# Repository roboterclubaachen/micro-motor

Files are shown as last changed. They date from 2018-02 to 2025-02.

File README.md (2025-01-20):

# µMotor: a motor controller for BLDC and DC motors up to 250W

µMotor (or micro-motor) is a motor controller PCB and software made to control any BLDC and DC motor up to 250W.

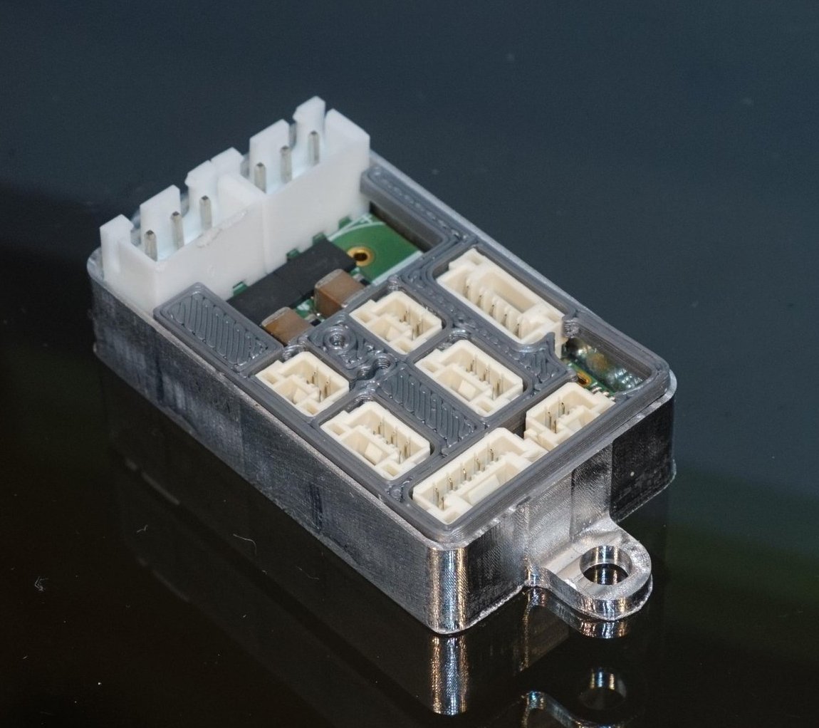
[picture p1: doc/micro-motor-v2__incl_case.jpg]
Image of micro-motor-v2 PCB in a milled aluminium case


The micro-motor is supplied with power and CAN bus via a single connector and can control the motor independently.
In addition, a limit switch can be read out and the temperature of the motor can be monitored.

Communication is done via Can-Bus using CANopen protocol.

The software is written using the [modm.io](https://modm.io/) framework and [librobots2](https://github.com/roboterclubaachen/librobots2).

For more information read the following blog posts about the project (in German):
* [µMotor: Idee](http://www.roboterclub.rwth-aachen.de/blog/2018/micro-motor-motorcontroller.html)
* [µMotor: Inbetriebnahme und Debugging](http://www.roboterclub.rwth-aachen.de/blog/2018/micro-motor-debugging-inbetriebnahme.html)
* [µMotor 2 - Teil 1: Konzept](http://www.roboterclub.rwth-aachen.de/blog/2019/micro-motor-2-teil-1.html)
* [µMotor 2 - Teil 2: Strommessung](http://www.roboterclub.rwth-aachen.de/blog/2019/micro-motor-2-teil-2.html)
* [µMotor 2 - Teil 3: Microcontroller & Stromversorgung](http://www.roboterclub.rwth-aachen.de/blog/2019/micro-motor-2-teil-3.html)
* [µMotor 2 - Teil 4: Strom- und Spannungsmessung mit ADC](https://www.roboterclub.rwth-aachen.de/blog/2020/micro-motor-2-teil-4.html)

## Technical data
* 3 phases (BLDC and DC motors)
* Approx. 10A per phase (with precise current measurement)
* 24V nominal operating voltage
* Adjustable cycle-by-cycle current limiting (short circuit protection)
* CAN bus
    * CAN-FD supported
    * CANopen protocoll (partial implemented)
* AB(I) incremental encoder connector
* Hall sensor connector
* Temperature sensor (NTC) connector
* Limit switch (GPIO) connector
* LEDs for status and diagnosis
* Configurable ID (from STM32 hardware ID)
* Easy to solder and assemble

## Status

PCBs *micro-motor-v1 (rev1)* and *macro-motor* are not supported anymore.

The second version *micro-motor-v2* is basically functional, software improvements are in progress.

PCB _micro-motor-v2.1_ is similar to _v2_, but with added RC filters at encoder connector,
added 1 µF capacitor to the STM32 _VREFBUF_ output and changed DC/DC converter modules (caused by component shortage).

Software at HEAD is compatible with micro-motor-v2.\[0,1,2\], however the correct version needs to be selected in the project.xml to account for hardware differences with "Board.v2_1" being compatible with v2.0, and v2.1 and "Board.v2_2" being compatible with v2.2.

## Folder structure

#### `kicad/pcb_name/`
* KiCad files of the PCBs

#### `STM32CubeMX/`
* Pinout configuration of the STM32 microcontrollers done with [STs CubeMX software](https://www.st.com/en/development-tools/stm32cubemx.html)

#### `tests/`
* Test software. Useful during PCB assembly

#### `app/`
* Main Software

#### `src/`
* Common files used between main software and tests.

## Notes

### On first boot
When first assembled the boards will be stuck inside the STM32 bootloader because BOOT0 is used as a GPIO pin.
This behaviour can be overwritten by setting an option byte: \
First read flash option byte:

    openocd -f interface/stlink.cfg -c "transport select hla_swd" -f target/stm32g4x.cfg -c "reset_config none" -c "init" -c "stm32g4x option_read 0 0x20" -c "shutdown"

Should respond 'Option Register: <0x40022020> = 0xffeff8aa' on a new PCB
or 'Option Register: <0x40022020> = 0xfbeff8aa' once the nSWBOOT0 bit is cleared. \
Clear the bit:

    openocd -f interface/stlink.cfg -c "transport select hla_swd" -f target/stm32g4x.cfg -c "reset_config none" -c "init" -c "stm32g4x option_write 0 0x20 0x00000000 0x04000000" -c "shutdown"

## License

Software is licensed under [GPLv3](LICENSE).
Hardware (PCB files, ...) is licensed under [CERN OHL v.1.2](LICENSE.hardware).

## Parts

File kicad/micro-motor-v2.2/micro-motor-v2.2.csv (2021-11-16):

Id | Designator | Package | Quantity | Designation | Supplier and ref
1 | U502 | Texas_SIL0010A_MicroSiP-10-1EP_3.8x3mm_P0.6mm_EP0.7x2.9mm | 1 | LMZM23601V5
2 | U501 | Texas_SIL0010A_MicroSiP-10-1EP_3.8x3mm_P0.6mm_EP0.7x2.9mm | 1 | LMZM23601V3
3 | R117,R116,R115 | R_0402_1005Metric | 3 | 10R
4 | C307 | C_0402_1005Metric | 1 | 1u
5 | C103,C102,C101 | C_0402_1005Metric | 3 | 10n
6 | U401 | QFN-32-1EP_5x5mm_P0.5mm_EP3.45x3.45mm | 1 | DRV8320S
7 | R114 | R_0402_1005Metric | 1 | 0
8 | C401 | CP_Radial_D10.0mm_P5.00mm | 1 | >10µ 35V
9 | C409,C408,C407 | C_1210_3225Metric | 3 | 22µ 35V 1210
10 | C412,C411,C410,C201,C403,C402,C306,C305,C304,C303,C302,C301 | C_0402_1005Metric | 12 | 100n
11 | R113,R112,R111,R401,R108,R101 | R_0402_1005Metric | 6 | 10k
12 | C502,C501,C504,C503 | C_0805_2012Metric | 4 | 22µ 10V 0805
13 | U404,U403,U402 | TSSOP-8_4.4x3mm_P0.65mm | 3 | INA240A2PW
14 | U301 | LQFP-48_7x7mm_P0.5mm | 1 | STM32G474CET6
15 | U201 | SOT-23-8 | 1 | TCAN332
16 | TP303 | TestPoint_Pad_D1.0mm | 1 | BK
17 | TP302 | TestPoint_Pad_D1.0mm | 1 | DAC1
18 | TP301 | TestPoint_Pad_D1.0mm | 1 | DAC2
19 | TP103 | TestPoint_Pad_D1.0mm | 1 | W
20 | TP102 | TestPoint_Pad_D1.0mm | 1 | V
21 | TP101 | TestPoint_Pad_D1.0mm | 1 | U
22 | R404,R403,R402 | R_0805_2012Metric | 3 | 5m
23 | R306,R305,R304,R110,R107,R105,R103 | R_0402_1005Metric | 7 | 1k
24 | R109,R106,R104,R102 | R_0402_1005Metric | 4 | 20k
25 | Q403,Q402,Q401 | DFN-12-2EP_3.3x5mm_Pitch0.65mm | 3 | FDMD82xx
26 | J303 | JST_GH_BM03B-GHS-TBT_1x03-1MP_P1.25mm_Vertical | 1 | SWD
27 | J302 | JST_GH_BM03B-GHS-TBT_1x03-1MP_P1.25mm_Vertical | 1 | UART
28 | J301 | USB_Micro-B_Molex-105133-0001 | 1 | USB
29 | J201 | JST_GH_BM02B-GHS-TBT_1x02-1MP_P1.25mm_Vertical | 1 | CAN
30 | J106 | JST_XH_B3B-XH-A_1x03_P2.50mm_Vertical | 1 | Motor
31 | J105 | JST_GH_BM02B-GHS-TBT_1x02-1MP_P1.25mm_Vertical | 1 | NTC
32 | J104 | JST_GH_BM05B-GHS-TBT_1x05-1MP_P1.25mm_Vertical | 1 | Encoder
33 | J103 | JST_GH_BM05B-GHS-TBT_1x05-1MP_P1.25mm_Vertical | 1 | Hall
34 | J102 | JST_GH_BM02B-GHS-TBT_1x02-1MP_P1.25mm_Vertical | 1 | SW
35 | J101 | JST_XH_B3B-XH-A_1x03_P2.50mm_Vertical | 1 | SUPPLY
36 | D303 | LED_0402_1005Metric | 1 | DAC2/green
37 | D302 | LED_0402_1005Metric | 1 | DAC1/red
38 | D301 | LED_0402_1005Metric | 1 | POWER/blue
39 | C406 | C_0402_1005Metric | 1 | 47n 50V X7R
40 | C405 | C_0603_1608Metric | 1 | 1µ 16V X7R
41 | C404 | C_0603_1608Metric | 1 | 1µ 6V3 X7R

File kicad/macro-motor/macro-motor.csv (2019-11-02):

Id | Designator | Package | Quantity | Designation | Supplier and ref
1 | REF**,REF**,REF**,REF** | MountingHole_3.2mm_M3_DIN965_Pad | 4 | MountingHole_3.2mm_M3_DIN965_Pad
2 | C201,C401,C601,C602,C603,C501,C206 | C_0402_1005Metric | 7 | 100n
3 | J604 | PinHeader_1x03_P2.54mm_Vertical | 1 | UART
4 | C101 | C_0603_1608Metric | 1 | 4µ7 16V
5 | C102,C103 | C_0402_1005Metric | 2 | 2µ2 6V3
6 | C301 | CP_Radial_D8.0mm_P3.50mm | 1 | >10µ 35V
7 | C302 | C_0603_1608Metric | 1 | 100n 50V
8 | C303 | C_0402_1005Metric | 1 | 100n 50V
9 | C304 | C_0402_1005Metric | 1 | 1µ 6V3 X7R
10 | C305 | C_0402_1005Metric | 1 | 1µ 16V X7R
11 | C306 | C_0402_1005Metric | 1 | 47n 50V X7R
12 | D601 | LED_0402_1005Metric | 1 | Blue
13 | D602 | LED_0402_1005Metric | 1 | Red
14 | J101 | PinHeader_1x05_P2.54mm_Vertical | 1 | CAN+PWR
15 | J102,J503 | Pin_D1.0mm_L10.0mm | 2 | 3V3
16 | J103 | Pin_D1.0mm_L10.0mm | 1 | 5V
17 | J104,J504,TP302 | Pin_D1.0mm_L10.0mm | 3 | GND
18 | J105 | Pin_D1.0mm_L10.0mm | 1 | Gpio
19 | J106,TP315,TP324 | Pin_D1.0mm_L10.0mm | 3 | U
20 | J107,TP314,TP323 | Pin_D1.0mm_L10.0mm | 3 | V
21 | J108,TP313,TP322 | Pin_D1.0mm_L10.0mm | 3 | W
22 | J109 | TerminalBlock_Phoenix_PT-1,5-3-3.5-H_1x03_P3.50mm_Horizontal | 1 | Conn_01x03_Female
23 | J202 | Pin_D1.0mm_L10.0mm | 1 | B
24 | J203 | Pin_D1.0mm_L10.0mm | 1 | A
25 | J301 | PinHeader_1x02_P2.54mm_Vertical | 1 | A
26 | J302 | PinHeader_1x02_P2.54mm_Vertical | 1 | B
27 | J303 | PinHeader_1x02_P2.54mm_Vertical | 1 | C
28 | J501 | Pin_D1.0mm_L10.0mm | 1 | SCL
29 | J502 | Pin_D1.0mm_L10.0mm | 1 | SDA
30 | J601 | PinHeader_1x03_P2.54mm_Vertical | 1 | SWD
31 | J605 | Pin_D1.0mm_L10.0mm | 1 | OP_INM
32 | J606 | Pin_D1.0mm_L10.0mm | 1 | OP_OUT
33 | J607 | Pin_D1.0mm_L10.0mm | 1 | PA0
34 | J608 | Pin_D1.0mm_L10.0mm | 1 | PH1
35 | J609 | Pin_D1.0mm_L10.0mm | 1 | PH0
36 | JP301 | SolderJumper-2_P1.3mm_Open_RoundedPad1.0x1.5mm | 1 | SPC
37 | JP302 | SolderJumper-2_P1.3mm_Open_RoundedPad1.0x1.5mm | 1 | SPB
38 | JP303 | SolderJumper-2_P1.3mm_Open_RoundedPad1.0x1.5mm | 1 | SPA
39 | Q301,Q302,Q303 | DFN-12-2EP_3.3x5mm_Pitch0.65mm | 3 | FDMD82xx
40 | R101,R301,R603,R605,R606,R607,R608 | R_0402_1005Metric | 7 | 10k
41 | R102,R103,R104,R601,R602,R604 | R_0402_1005Metric | 6 | 1k
42 | R105,R106,R107 | R_0402_1005Metric | 3 | 20k
43 | R302,R303,R304 | R_0805_2012Metric | 3 | 5m
44 | R501,R502 | R_0402_1005Metric | 2 | 4k7
45 | TP303,TP304 | Pin_D1.0mm_L10.0mm | 2 | UP
46 | TP305 | Pin_D1.0mm_L10.0mm | 1 | VP
47 | TP306 | Pin_D1.0mm_L10.0mm | 1 | VN
48 | TP307 | Pin_D1.0mm_L10.0mm | 1 | WP
49 | TP308 | Pin_D1.0mm_L10.0mm | 1 | WN
50 | TP309 | Pin_D1.0mm_L10.0mm | 1 | MOSI
51 | TP310 | Pin_D1.0mm_L10.0mm | 1 | MISO
52 | TP311 | Pin_D1.0mm_L10.0mm | 1 | SCK
53 | TP312 | Pin_D1.0mm_L10.0mm | 1 | ~CS
54 | TP316 | Pin_D1.0mm_L10.0mm | 1 | GH_U
55 | TP317 | Pin_D1.0mm_L10.0mm | 1 | GL_U
56 | TP318 | Pin_D1.0mm_L10.0mm | 1 | GH_W
57 | TP319 | Pin_D1.0mm_L10.0mm | 1 | GL_W
58 | TP320 | Pin_D1.0mm_L10.0mm | 1 | GH_V
59 | TP321 | Pin_D1.0mm_L10.0mm | 1 | GL_V
60 | U101 | WLCSP-6_1.4x1.0mm_P0.4mm | 1 | ADP7112ACBZ-3.3-R7
61 | U102 | WLCSP-6_1.4x1.0mm_P0.4mm | 1 | ADP7112ACBZ-5.0-R7
62 | U301 | QFN-40-1EP_6x6mm_P0.5mm_EP4.6x4.6mm | 1 | DRV8323S
63 | U401 | SOT-23-8 | 1 | TCAN330
64 | U501 | WCSP-8_1.6x1.6mm_P0.5mm | 1 | TMP006
65 | U601 | QFN-48-1EP_7x7mm_P0.5mm_EP5.6x5.6mm | 1 | STM32L433C(B-C)Ux_u
66 | J110 | PinHeader_1x05_P2.54mm_Vertical | 1 | HALL
67 | J204 | PinHeader_1x06_P2.54mm_Vertical | 1 | Encoder
68 | R203,R204,R205,R206 | R_0402_1005Metric | 4 | 47k
69 | TP301 | Pin_D1.0mm_L10.0mm | 1 | +24V
70 | J111 | Pin_D1.0mm_L10.0mm | 1 | Fault
71 | R108 | R_0402_1005Metric | 1 | (10k)
72 | C202,C203,C204,C205 | C_0402_1005Metric | 4 | (2n7)
73 | RN201 | EXB18V | 1 | (2k7)
74 | RN202 | EXB18V | 1 | (100)
75 | G*** | aisler-logo | 1 | LOGO
76 | G*** | rca-logo | 1 | LOGO
77 | U201,U202 | SOT-23-5 | 2 | ISL3280E

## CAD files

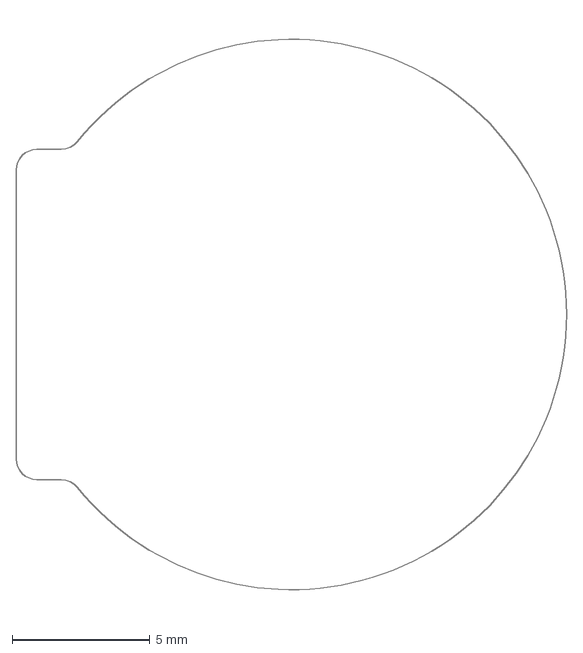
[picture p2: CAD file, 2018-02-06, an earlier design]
kicad/micro-motor-v1/PCB_Outline_rev1.dxf
20.0 x 21.7 mm

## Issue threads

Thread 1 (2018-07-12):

Bug in PCB rev1 // TODO for PCB rev2

rleh, 2018-07-12:
* [ ] SPI MISO pull-up resistor (10k)
* [ ] ~I²C pull-up resistors (4k7)~
* [ ] Analog (NTC) temperature sensor instead of I²C
* [ ] Measure (ADC) or detect (GPIO) the input voltage from STM32
* [ ] Remove integrated magnet encoder
* [ ] ~THT terminals~ Small SMD connectors (e.g. [JST GH](https://jst.de/product-family/show/89/gh))
  * [ ] Encoder (A, B, I, GND, 5V|3.3V)
  * [ ] Hall sensor (U, V, W, GND, 5V|3.3V)
  * [ ] End switch
  * [ ] CAN?
* [ ] Power connectors (e.g. [JST XH](https://jst.de/product-family/show/184/xh))
  * [ ]  Power supply: 20V, 6V, GND; >=5A
  * [ ] Combined with CAN?
* [ ] Use MOSFET R_dson (4..6mΩ) instead of 5mΩ shunt resistor?
* [ ] NCP4623 is *NRND* -> Replacement: [ADP7112](http://www.analog.com/media/en/technical-documentation/data-sheets/ADP7112.pdf) *1mm × 1.2mm, 6-ball WLCSP*
  * [ ] Discussion: [Fully integrated switching regulator TPS82150](http://www.ti.com/product/TPS82150) for 5V (and 3.3V)?
* [ ] Mechanical dimensions: ~Round~ Rectangular shape, approx. 15x25mm²

To be continued...

rleh, 2021-07-31:
Done.

Closed 2021-07-31.

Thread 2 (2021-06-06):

I want to adapt this for 2 to 5 hp motor

bkrajendra, 2021-06-06:
I want to adapt this for 2 to 5 hp motor.
I am planning to develop a solar powered BLDC motor pump without using any batteries.
SOPV   + MPPT tracking + BLDV driver-> BLDC Motor.

What changes need to be done to handle these voltage levels?

rleh, 2021-06-07:
Hi @bkrajendra!

> I want to adapt this for 2 to 5 hp motor.
> I am planning to develop a solar powered BLDC motor pump without using any batteries.
> SOPV + MPPT tracking + BLDV driver-> BLDC Motor.

Could be possible.

> What changes need to be done to handle these voltage levels?

With which voltage will your system run? Solar systems are available from 5V to >1kV...

bkrajendra, 2021-06-07:
Thank you for the quick reply.
A typical solar panel I was targeting was about 250Watt, 37.7 V, 9Amp max current
The target motors are about 1 to 3HP.

I might be wrong with the few details, but the ultimate aim is to drive up to 3hp (max 5hp) BLDC motors directly through Solar PV.

rleh, 2021-06-07:
> A typical solar panel I was targeting was about 250Watt, 37.7 V, 9Amp max current
> The target motors are about 1 to 3HP.

But 250W != 3HP, so you somehow have to connect multiple panels together. Willy they be in series or parallel connection?

As far as I remember, most components which are connected to the "+24V" voltage rail in the schematics are 60V rated, or at least 40V rated.
Assuming a system voltage of 37.7V, the 60V components should be fine, any 40V or lower rated chips have to be replaced.
The best thing to do is to go through the schematic and look at all the components.

You also have to replace al least the MOSFETs with larger ones.

Also note the separate "Logic" voltage supply (+6V to +12V used in past Roboterclub applications), which is down-converted to +3.3V by the TPS82150 integrated DC/DC converter chip. If you want to use a single supply you would also have to replace that chip.

---

Maybe it could be easier to use/adapt another open source motor controller for your application, that was initial designed for higher power and voltages, like [VESC](https://vesc-project.com/) (https://github.com/vedderb/bldc-hardware) or https://github.com/SDI-SoftwareDefinedInverter/TAPAS?!

Closed 2021-07-31.

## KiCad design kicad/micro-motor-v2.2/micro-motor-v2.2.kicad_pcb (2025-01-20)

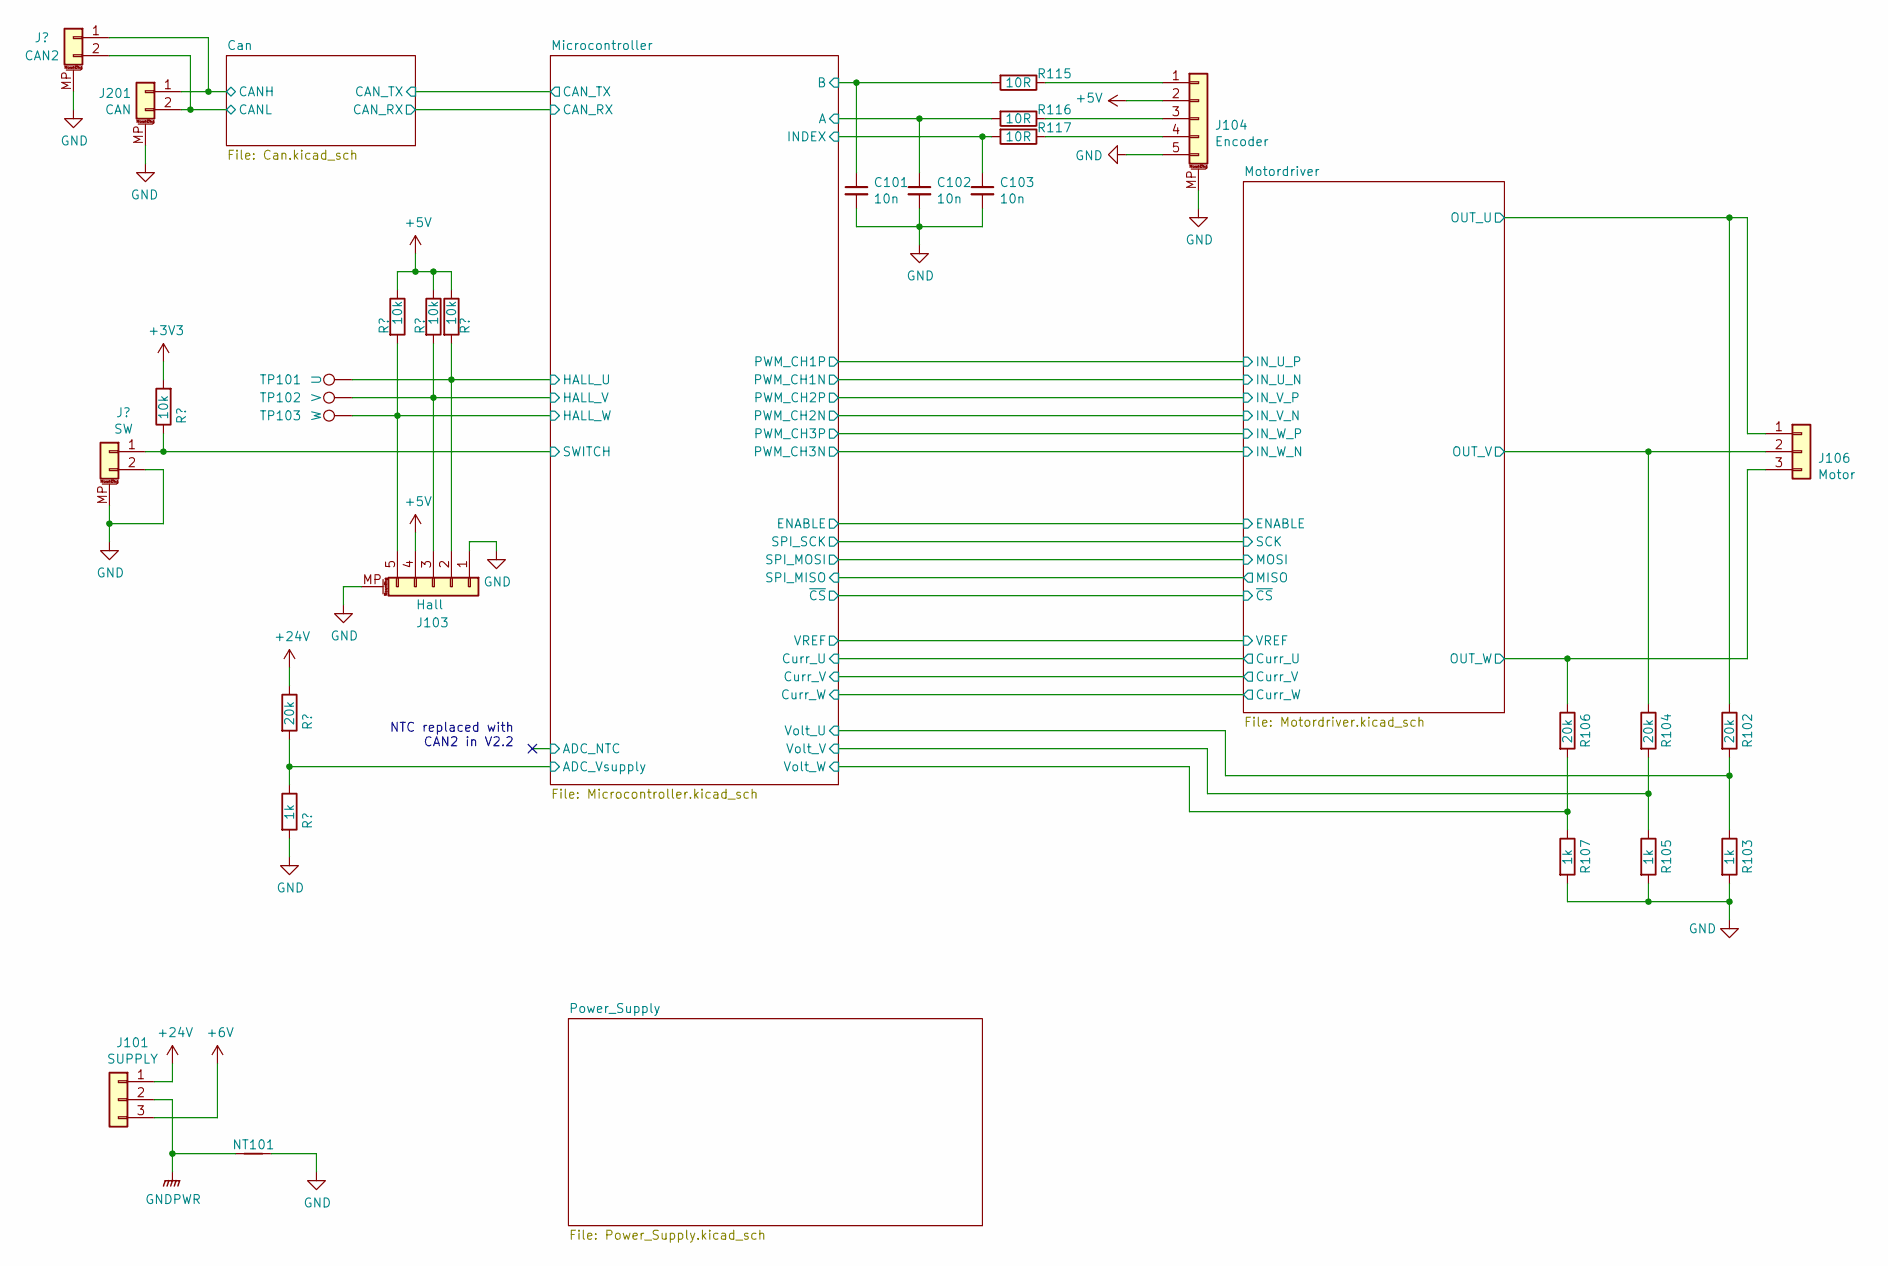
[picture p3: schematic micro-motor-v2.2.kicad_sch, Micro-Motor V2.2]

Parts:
C101, C102, C103: 10n; C_0402_1005Metric
J101: SUPPLY; JST_XH_B3B-XH-A_1x03_P2.50mm_Vertical
J102: SW; JST_GH_BM02B-GHS-TBT_1x02-1MP_P1.25mm_Vertical
J103: Hall; JST_GH_BM05B-GHS-TBT_1x05-1MP_P1.25mm_Vertical
J104: Encoder; JST_GH_BM05B-GHS-TBT_1x05-1MP_P1.25mm_Vertical
J105: CAN2; JST_GH_BM02B-GHS-TBT_1x02-1MP_P1.25mm_Vertical
J106: Motor; JST_XH_B3B-XH-A_1x03_P2.50mm_Vertical
J201: CAN; JST_GH_BM02B-GHS-TBT_1x02-1MP_P1.25mm_Vertical
NT101: NetTie_2; NetTie-2_SMD_Pad0.5mm
R101, R111, R112, R113: 10k; R_0402_1005Metric
R102, R104, R106, R109: 20k; R_0402_1005Metric
R103, R105, R107, R110: 1k; R_0402_1005Metric
R115, R116, R117: 10R; R_0402_1005Metric
TP101: U; TestPoint_Pad_D1.0mm
TP102: V; TestPoint_Pad_D1.0mm
TP103: W; TestPoint_Pad_D1.0mm

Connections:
+3V3: R101.2; also elsewhere on the board
+5V: J103.4, J104.2, R111.1, R112.1, R113.1; also elsewhere on the board
+6V: J101.3; also elsewhere on the board
+24V: J101.1, R109.1; also elsewhere on the board
/Can/CANH: J105.1; also elsewhere on the board
/Can/CANL: J105.2; also elsewhere on the board
/Microcontroller/A: C102.1, R116.2; also elsewhere on the board
/Microcontroller/ADC_Vsupply: R109.2, R110.1; also elsewhere on the board
/Microcontroller/B: C101.1, R115.2; also elsewhere on the board
/Microcontroller/HALL_U: J103.2, R113.2, TP101.1; also elsewhere on the board
/Microcontroller/HALL_V: J103.3, R112.2, TP102.1; also elsewhere on the board
/Microcontroller/HALL_W: J103.5, R111.2, TP103.1; also elsewhere on the board
/Microcontroller/INDEX: C103.1, R117.2; also elsewhere on the board
/Microcontroller/SWITCH: J102.1, R101.1; also elsewhere on the board
/Microcontroller/Volt_U: R102.2, R103.1; also elsewhere on the board
/Microcontroller/Volt_V: R104.2, R105.1; also elsewhere on the board
/Microcontroller/Volt_W: R106.2, R107.1; also elsewhere on the board
/Motordriver/OUT_U: J106.1, R102.1; also elsewhere on the board
/Motordriver/OUT_V: J106.2, R104.1; also elsewhere on the board
/Motordriver/OUT_W: J106.3, R106.1; also elsewhere on the board
GND: C101.2, C102.2, C103.2, J102.2, J102.MP (MountPin), J103.1, J103.MP (MountPin), J104.5, J104.MP (MountPin), J105.MP (MountPin), NT101.2, R103.2, R105.2, R107.2, R110.2; also elsewhere on the board
GNDPWR: J101.2, NT101.1; also elsewhere on the board
unnamed: J104.1, R115.1
unnamed: J104.3, R116.1
unnamed: J104.4, R117.1

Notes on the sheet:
NTC replaced with CAN2 in V2.2

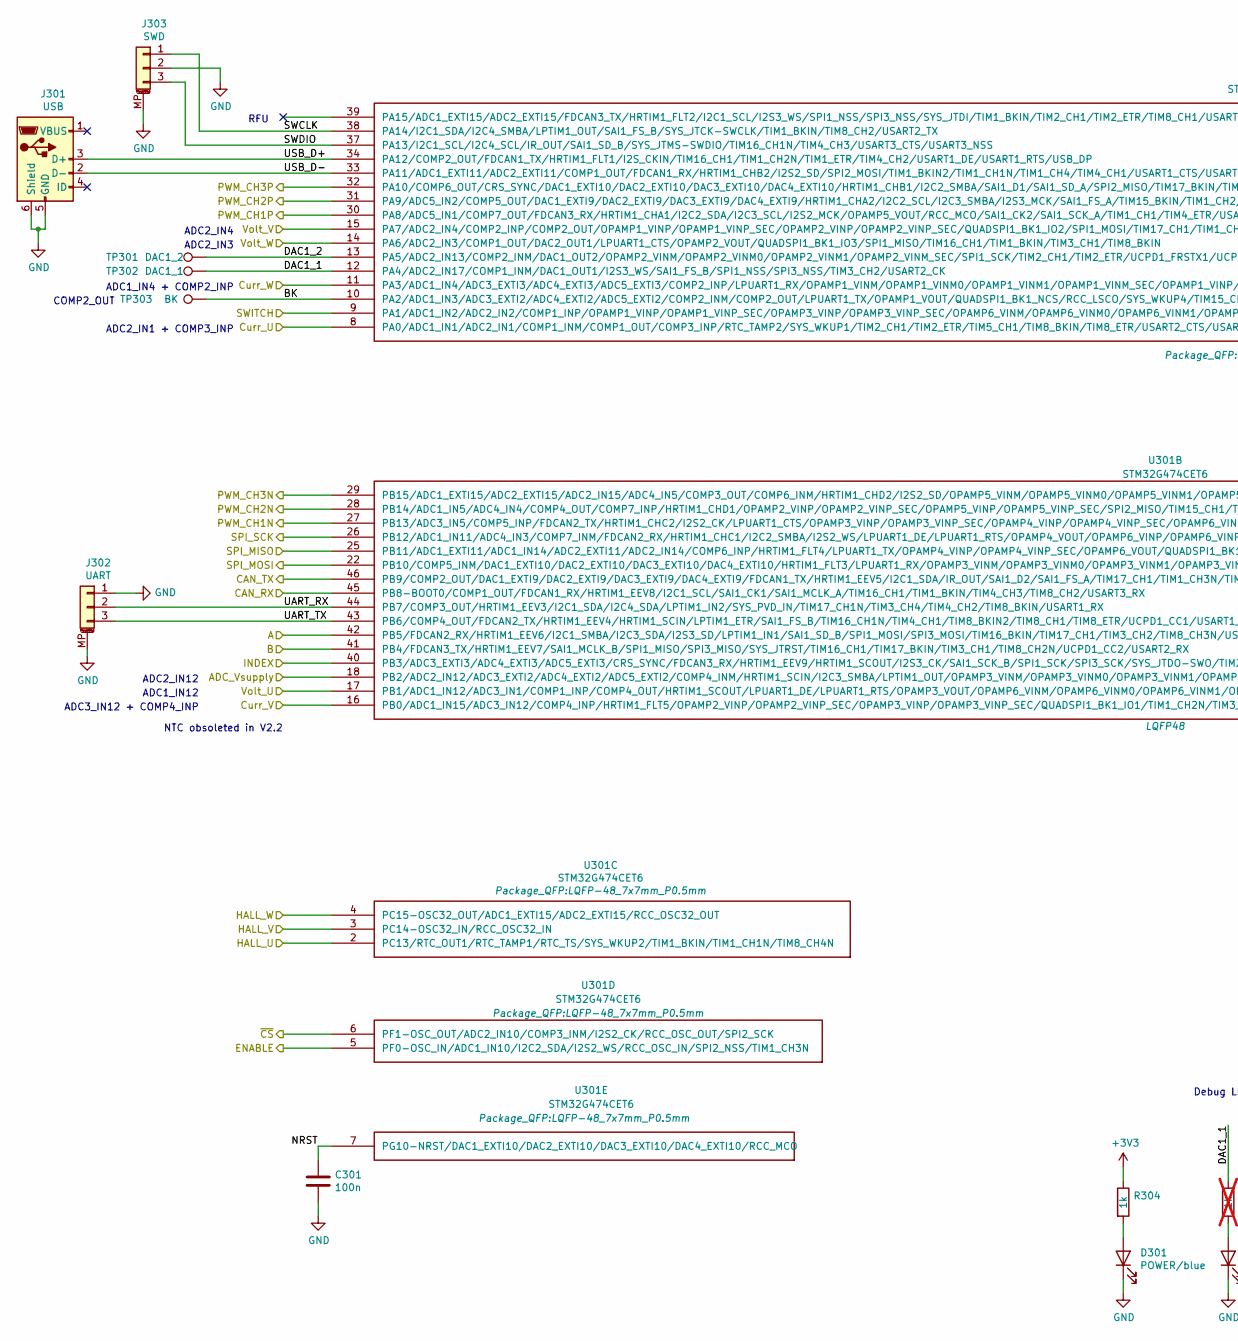
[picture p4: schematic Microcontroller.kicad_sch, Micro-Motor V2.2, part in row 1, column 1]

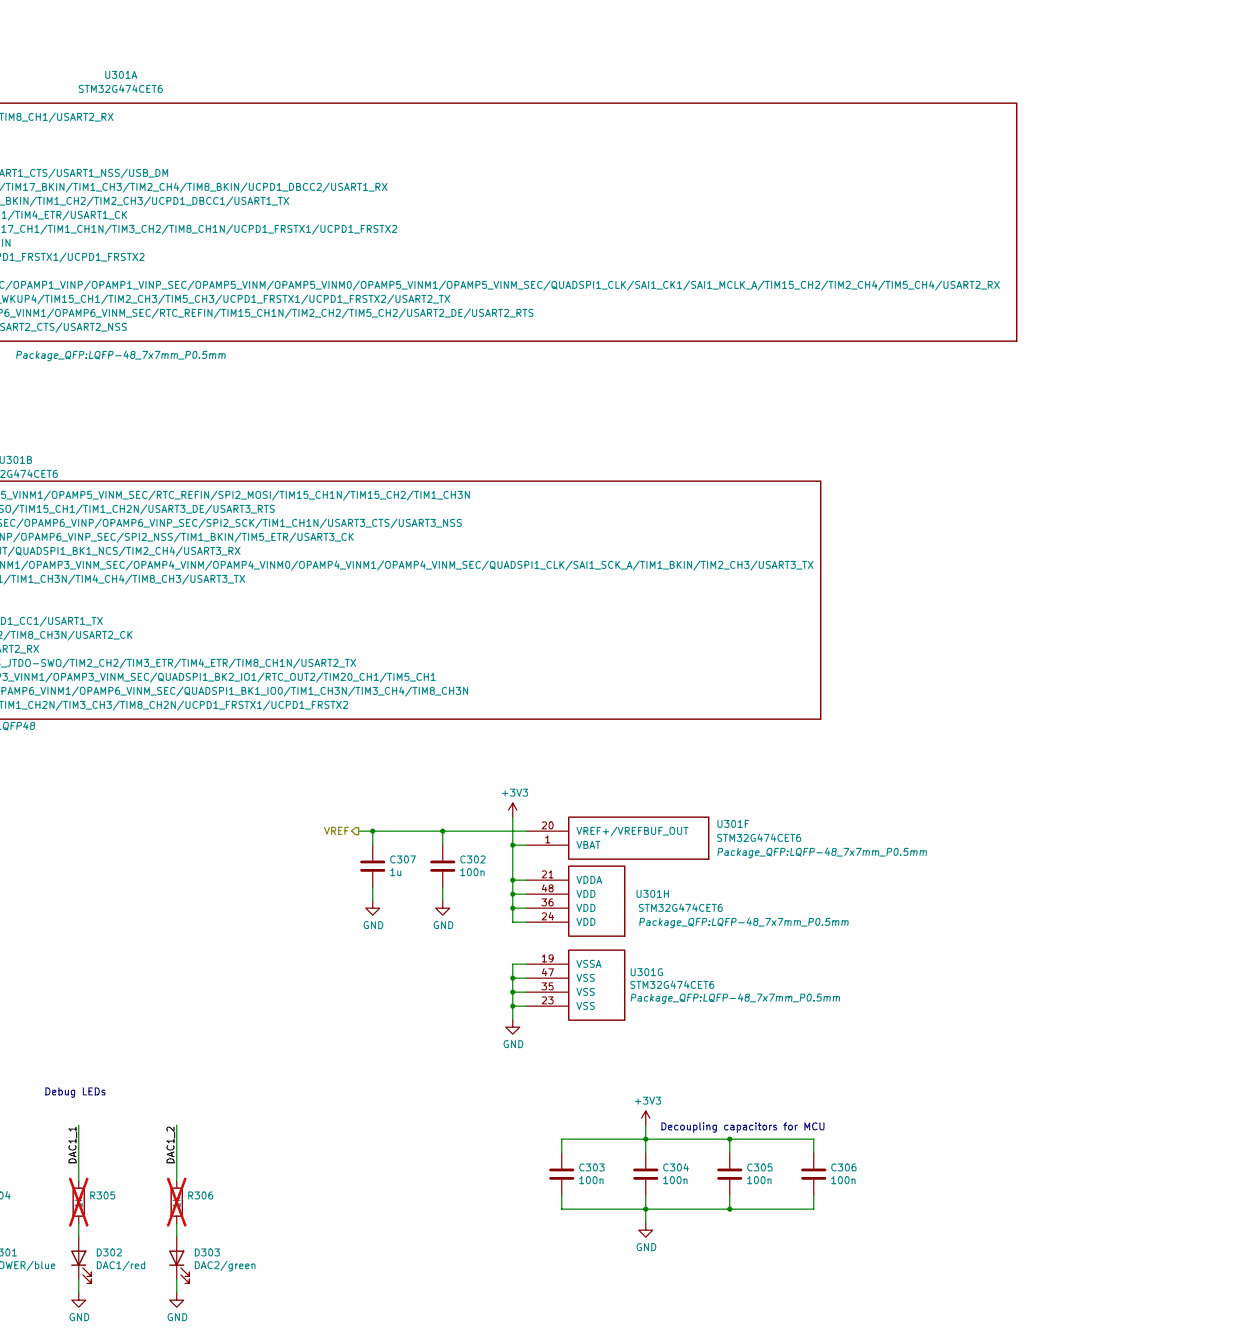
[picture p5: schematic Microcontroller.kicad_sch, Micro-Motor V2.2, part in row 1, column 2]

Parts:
C301, C302, C303, C304, C305, C306: 100n; C_0402_1005Metric
C307: 1u; C_0402_1005Metric
D301: POWER/blue; LED_0402_1005Metric
D302: DAC1/red; LED_0402_1005Metric
D303: DAC2/green; LED_0402_1005Metric
J301: USB; USB_Micro-B_Molex-105133-0001
J302: UART; JST_GH_BM03B-GHS-TBT_1x03-1MP_P1.25mm_Vertical
J303: SWD; JST_GH_BM03B-GHS-TBT_1x03-1MP_P1.25mm_Vertical
R304: 1k; R_0402_1005Metric
R305, R306: 1k; R_0402_1005Metric; not fitted
TP301: DAC1_2; TestPoint_Pad_D1.0mm
TP302: DAC1_1; TestPoint_Pad_D1.0mm
TP303: BK; TestPoint_Pad_D1.0mm
U301: STM32G474CET6; LQFP-48_7x7mm_P0.5mm

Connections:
+3V3: C303.1, C304.1, C305.1, C306.1, R304.1, U301.1 (VBAT), U301.21 (VDDA), U301.24 (VDD), U301.36 (VDD), U301.48 (VDD); also elsewhere on the board
/Can/CAN_RX: U301.45 (PB8-BOOT0/COMP1_OUT/FDCAN1_RX/HRTIM1_EE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); also elsewhere on the board
/Can/CAN_TX: U301.46 (PB9/COMP2_OUT/DAC1_EXTI9/DAC2_EXTI9/DAC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); also elsewhere on the board
/Microcontroller/A: U301.42 (PB5/FDCAN2_RX/HRTIM1_EEV6/I2C1_SMBA/I2C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); also elsewhere on the board
/Microcontroller/ADC_Vsupply: U301.18 (PB2/ADC2_IN12/ADC3_EXTI2/ADC4_EXTI2/ADC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); also elsewhere on the board
/Microcontroller/B: U301.41 (PB4/FDCAN3_TX/HRTIM1_EEV7/SAI1_MCLK_B/S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); also elsewhere on the board
/Microcontroller/BK: TP303.1, U301.10 (PA2/ADC1_IN3/ADC3_EXTI2/ADC4_EXTI2/ADC5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)
/Microcontroller/Curr_U: U301.8 (PA0/ADC1_IN1/ADC2_IN1/COMP1_INM/COMP1_O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); also elsewhere on the board
/Microcontroller/Curr_V: U301.16 (PB0/ADC1_IN15/ADC3_IN12/COMP4_INP/HRTIM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); also elsewhere on the board
/Microcontroller/Curr_W: U301.11 (PA3/ADC1_IN4/ADC3_EXTI3/ADC4_EXTI3/ADC5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); also elsewhere on the board
/Microcontroller/DAC1_1: R305.1, TP302.1, U301.12 (PA4/ADC2_IN17/COMP1_INM/DAC1_OUT1/I2S3_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)
/Microcontroller/DAC1_2: R306.1, TP301.1, U301.13 (PA5/ADC2_IN13/COMP2_INM/DAC1_OUT2/OPAMP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)
/Microcontroller/ENABLE: U301.5 (PF0-OSC_IN/ADC1_IN10/I2C2_SDA/I2S2_WS/R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); also elsewhere on the board
/Microcontroller/HALL_U: U301.2 (PC13/RTC_OUT1/RTC_TAMP1/RTC_TS/SYS_WKUP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); also elsewhere on the board
/Microcontroller/HALL_V: U301.3 (PC14-OSC32_IN/RCC_OSC32_IN); also elsewhere on the board
/Microcontroller/HALL_W: U301.4 (PC15-OSC32_OUT/ADC1_EXTI15/ADC2_EXTI15/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); also elsewhere on the board
/Microcontroller/INDEX: U301.40 (PB3/ADC3_EXTI3/ADC4_EXTI3/ADC5_EXTI3/CR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); also elsewhere on the board
/Microcontroller/NRST: C301.1, U301.7 (PG10-NRST/DAC1_EXTI10/DAC2_EXTI10/DAC3_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)
/Microcontroller/PWM_CH1N: U301.27 (PB13/ADC3_IN5/COMP5_INP/FDCAN2_TX/HRTIM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); also elsewhere on the board
/Microcontroller/PWM_CH1P: U301.30 (PA8/ADC5_IN1/COMP7_OUT/FDCAN3_RX/HRTIM1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); also elsewhere on the board
/Microcontroller/PWM_CH2N: U301.28 (PB14/ADC1_IN5/ADC4_IN4/COMP4_OUT/COMP7_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); also elsewhere on the board
/Microcontroller/PWM_CH2P: U301.31 (PA9/ADC5_IN2/COMP5_OUT/DAC1_EXTI9/DAC2_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); also elsewhere on the board
/Microcontroller/PWM_CH3N: U301.29 (PB15/ADC1_EXTI15/ADC2_EXTI15/ADC2_IN15/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); also elsewhere on the board
/Microcontroller/PWM_CH3P: U301.32 (PA10/COMP6_OUT/CRS_SYNC/DAC1_EXTI10/DAC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); also elsewhere on the board
/Microcontroller/SPI_MISO: U301.25 (PB11/ADC1_EXTI11/ADC1_IN14/ADC2_EXTI11/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); also elsewhere on the board
/Microcontroller/SPI_MOSI: U301.22 (PB10/COMP5_INM/DAC1_EXTI10/DAC2_EXTI10/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); also elsewhere on the board
/Microcontroller/SPI_SCK: U301.26 (PB12/ADC1_IN11/ADC4_IN3/COMP7_INM/FDCAN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); also elsewhere on the board
/Microcontroller/SWCLK: J303.1, U301.38 (PA14/I2C1_SDA/I2C4_SMBA/LPTIM1_OUT/SAI1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)
/Microcontroller/SWDIO: J303.3, U301.37 (PA13/I2C1_SCL/I2C4_SCL/IR_OUT/SAI1_SD_B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)
/Microcontroller/SWITCH: U301.9 (PA1/ADC1_IN2/ADC2_IN2/COMP1_INP/OPAMP1_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); also elsewhere on the board
/Microcontroller/UART_RX: J302.2, U301.44 (PB7/COMP3_OUT/HRTIM1_EEV3/I2C1_SDA/I2C4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)
/Microcontroller/UART_TX: J302.3, U301.43 (PB6/COMP4_OUT/FDCAN2_TX/HRTIM1_EEV4/HRT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)
/Microcontroller/USB_D+: J301.3 (D+), U301.34 (PA12/COMP2_OUT/FDCAN1_TX/HRTIM1_FLT1/I2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)
/Microcontroller/USB_D-: J301.2 (D-), U301.33 (PA11/ADC1_EXTI11/ADC2_EXTI11/COMP1_OUT/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)
/Microcontroller/VREF: C302.1, C307.1, U301.20 (VREF+/VREFBUF_OUT); also elsewhere on the board
/Microcontroller/Volt_U: U301.17 (PB1/ADC1_IN12/ADC3_IN1/COMP1_INP/COMP4_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); also elsewhere on the board
/Microcontroller/Volt_V: U301.15 (PA7/ADC2_IN4/COMP2_INP/COMP2_OUT/OPAMP1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); also elsewhere on the board
/Microcontroller/Volt_W: U301.14 (PA6/ADC2_IN3/COMP1_OUT/DAC2_OUT1/LPUART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); also elsewhere on the board
/Microcontroller/~CS: U301.6 (PF1-OSC_OUT/ADC2_IN10/COMP3_INM/I2S2_CK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); also elsewhere on the board
GND: C301.2, C302.2, C303.2, C304.2, C305.2, C306.2, C307.2, D301.1 (K), D302.1 (K), D303.1 (K), J301.5 (GND), J301.6 (Shield), J302.1, J302.MP (MountPin), J303.2, J303.MP (MountPin), U301.19 (VSSA), U301.23 (VSS), U301.35 (VSS), U301.47 (VSS); also elsewhere on the board
unnamed: D301.2 (A), R304.2
unnamed: D302.2 (A), R305.2
unnamed: D303.2 (A), R306.2

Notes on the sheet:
ADC1_IN4 + COMP2_INP
ADC2_IN3
ADC2_IN12
ADC3_IN12 + COMP4_INP
ADC2_IN4
NTC obsoleted in V2.2
Debug LEDs
Decoupling capacitors for MCU
COMP2_OUT
RFU
ADC1_IN12
ADC2_IN1 + COMP3_INP

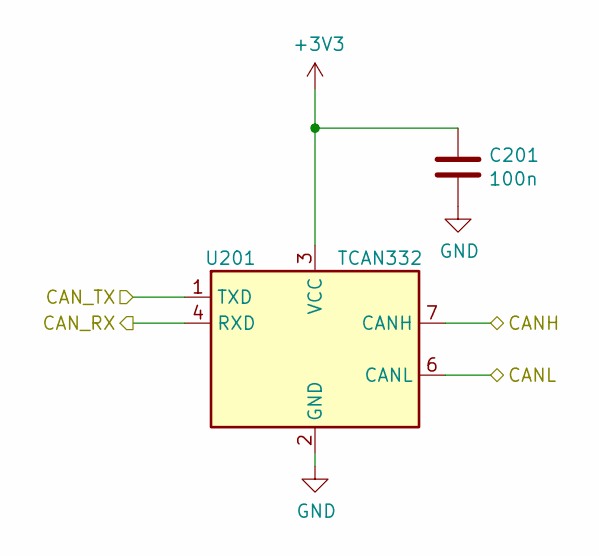
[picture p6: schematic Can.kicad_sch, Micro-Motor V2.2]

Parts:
C201: 100n; C_0402_1005Metric
U201: TCAN332; SOT-23-8

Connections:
+3V3: C201.1, U201.3 (VCC); also elsewhere on the board
/Can/CANH: U201.7 (CANH); also elsewhere on the board
/Can/CANL: U201.6 (CANL); also elsewhere on the board
/Can/CAN_RX: U201.4 (RXD); also elsewhere on the board
/Can/CAN_TX: U201.1 (TXD); also elsewhere on the board
GND: C201.2, U201.2 (GND); also elsewhere on the board

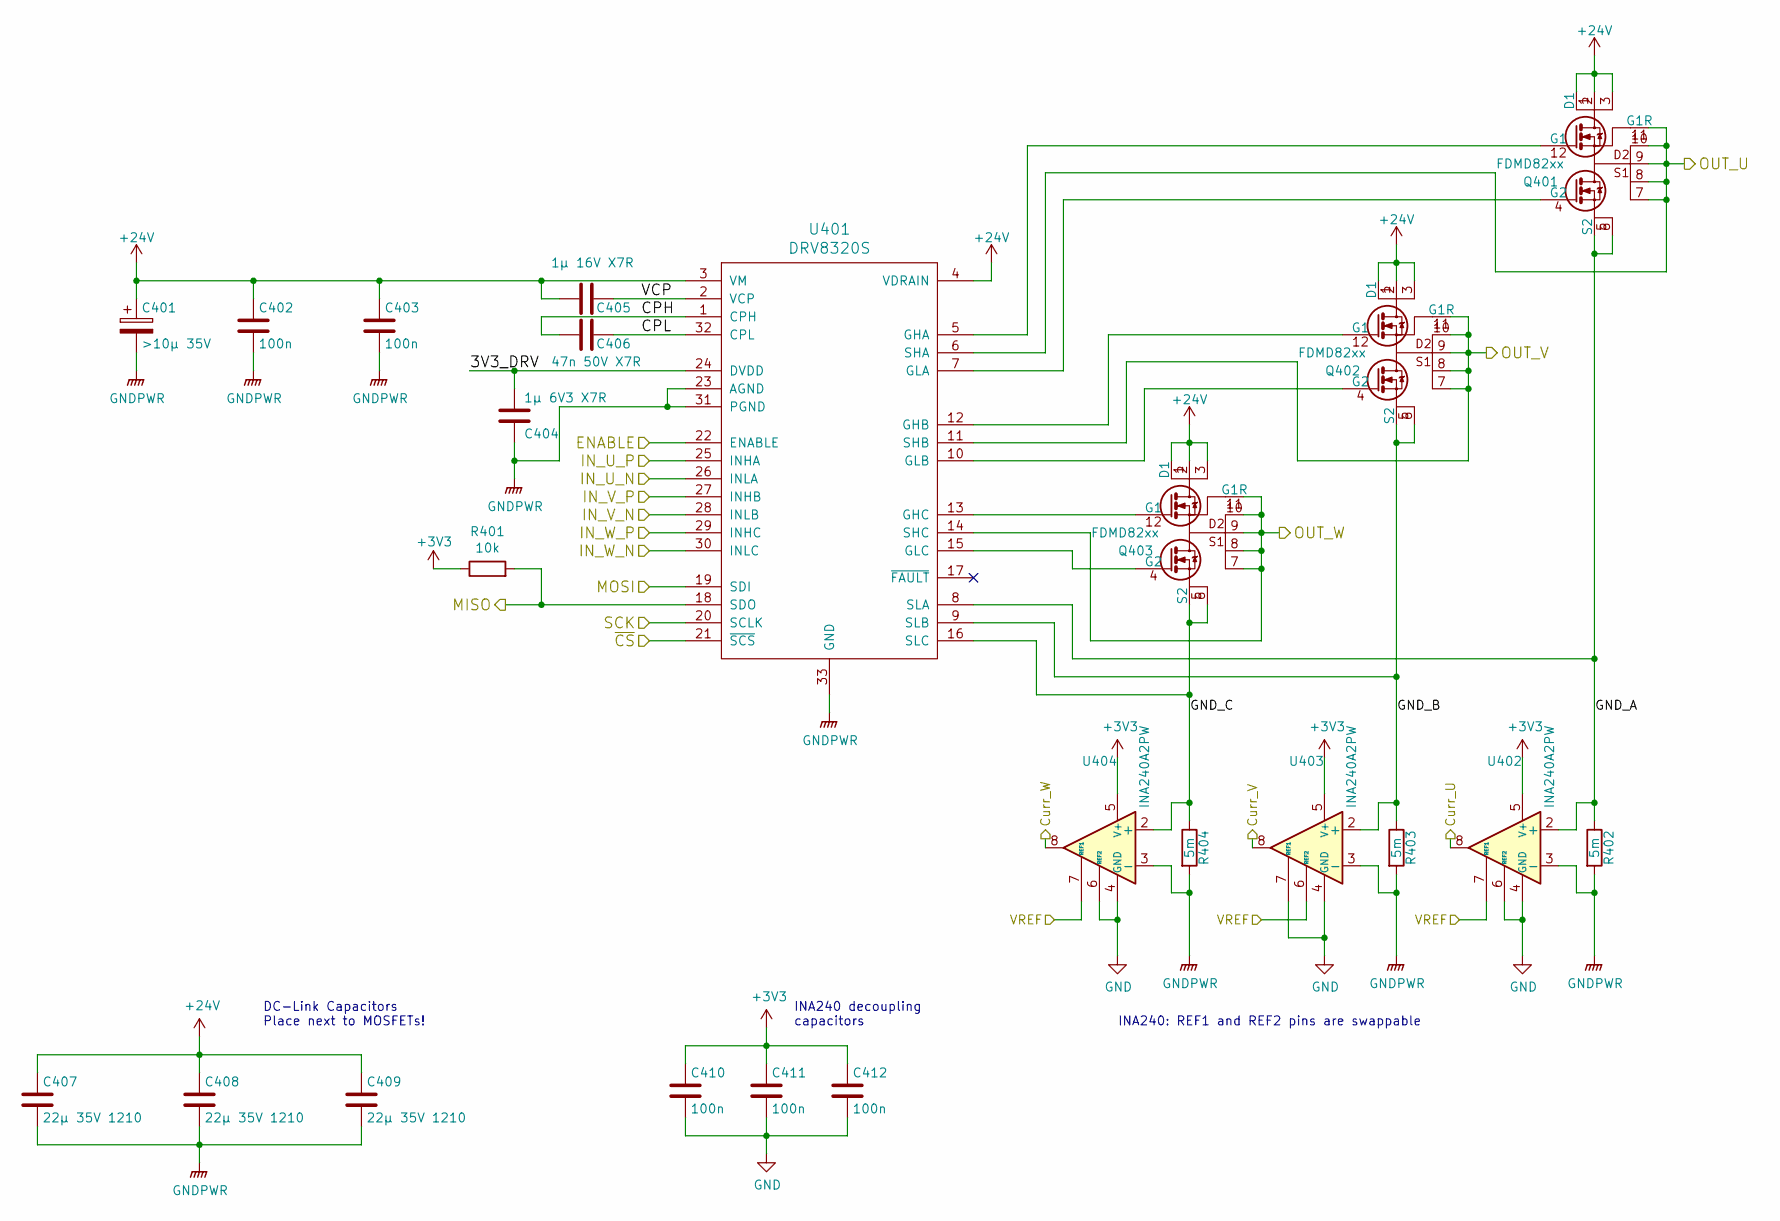
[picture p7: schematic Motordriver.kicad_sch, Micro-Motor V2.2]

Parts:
C401: >10µ 35V; CP_Radial_D10.0mm_P5.00mm
C402, C403, C410, C411, C412: 100n; C_0402_1005Metric
C404: 1µ 6V3 X7R; C_0603_1608Metric
C405: 1µ 16V X7R; C_0603_1608Metric
C406: 47n 50V X7R; C_0402_1005Metric
C407, C408, C409: 22µ 35V 1210; C_1210_3225Metric
Q401, Q402, Q403: FDMD82xx; DFN-12-2EP_3.3x5mm_Pitch0.65mm
R401: 10k; R_0402_1005Metric
R402, R403, R404: 5m; R_0805_2012Metric
U401: DRV8320S; QFN-32-1EP_5x5mm_P0.5mm_EP3.45x3.45mm
U402, U403, U404: INA240A2PW; TSSOP-8_4.4x3mm_P0.65mm

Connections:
+3V3: C410.1, C411.1, C412.1, R401.1, U402.5 (V+), U403.5 (V+), U404.5 (V+); also elsewhere on the board
+24V: C401.1, C402.1, C403.1, C405.2, C407.1, C408.1, C409.1, Q401.1 (D1), Q401.2, Q401.3, Q401.13 (D1), Q402.1 (D1), Q402.2, Q402.3, Q402.13 (D1), Q403.1 (D1), Q403.2, Q403.3, Q403.13 (D1), U401.3 (VM), U401.4 (VDRAIN); also elsewhere on the board
/Microcontroller/Curr_U: U402.8; also elsewhere on the board
/Microcontroller/Curr_V: U403.8; also elsewhere on the board
/Microcontroller/Curr_W: U404.8; also elsewhere on the board
/Microcontroller/ENABLE: U401.22 (ENABLE); also elsewhere on the board
/Microcontroller/PWM_CH1N: U401.26 (INLA); also elsewhere on the board
/Microcontroller/PWM_CH1P: U401.25 (INHA); also elsewhere on the board
/Microcontroller/PWM_CH2N: U401.28 (INLB); also elsewhere on the board
/Microcontroller/PWM_CH2P: U401.27 (INHB); also elsewhere on the board
/Microcontroller/PWM_CH3N: U401.30 (INLC); also elsewhere on the board
/Microcontroller/PWM_CH3P: U401.29 (INHC); also elsewhere on the board
/Microcontroller/SPI_MISO: R401.2, U401.18 (SDO); also elsewhere on the board
/Microcontroller/SPI_MOSI: U401.19 (SDI); also elsewhere on the board
/Microcontroller/SPI_SCK: U401.20 (SCLK); also elsewhere on the board
/Microcontroller/VREF: U402.7 (REF1), U403.6 (REF2), U404.7 (REF1); also elsewhere on the board
/Microcontroller/~CS: U401.21 (~SCS); also elsewhere on the board
/Motordriver/3V3_DRV: C404.1, U401.24 (DVDD)
/Motordriver/CPH: C406.2, U401.1 (CPH)
/Motordriver/CPL: C406.1, U401.32 (CPL)
/Motordriver/GND_A: Q401.5 (S2), Q401.6, Q401.14 (S2), R402.1, U401.8 (SLA), U402.2 (+)
/Motordriver/GND_B: Q402.5 (S2), Q402.6, Q402.14 (S2), R403.1, U401.9 (SLB), U403.2 (+)
/Motordriver/GND_C: Q403.5 (S2), Q403.6, Q403.14 (S2), R404.1, U401.16 (SLC), U404.2 (+)
/Motordriver/OUT_U: Q401.7, Q401.8, Q401.9, Q401.10, Q401.11 (G1R), U401.6 (SHA); also elsewhere on the board
/Motordriver/OUT_V: Q402.7, Q402.8, Q402.9, Q402.10, Q402.11 (G1R), U401.11 (SHB); also elsewhere on the board
/Motordriver/OUT_W: Q403.7, Q403.8, Q403.9, Q403.10, Q403.11 (G1R), U401.14 (SHC); also elsewhere on the board
/Motordriver/VCP: C405.1, U401.2 (VCP)
GND: C410.2, C411.2, C412.2, U402.1 (GND), U402.4 (GND), U402.6 (REF2), U403.1 (GND), U403.4 (GND), U403.7 (REF1), U404.1 (GND), U404.4 (GND), U404.6 (REF2); also elsewhere on the board
GNDPWR: C401.2, C402.2, C403.2, C404.2, C407.2, C408.2, C409.2, R402.2, R403.2, R404.2, U401.23 (AGND), U401.31 (PGND), U401.33 (GND), U402.3 (-), U403.3 (-), U404.3 (-); also elsewhere on the board
unnamed: Q401.12 (G1), U401.5 (GHA)
unnamed: Q401.4 (G2), U401.7 (GLA)
unnamed: Q402.12 (G1), U401.12 (GHB)
unnamed: Q402.4 (G2), U401.10 (GLB)
unnamed: Q403.12 (G1), U401.13 (GHC)
unnamed: Q403.4 (G2), U401.15 (GLC)

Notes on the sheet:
DC-Link Capacitors Place next to MOSFETs!
INA240 decoupling capacitors
INA240: REF1 and REF2 pins are swappable

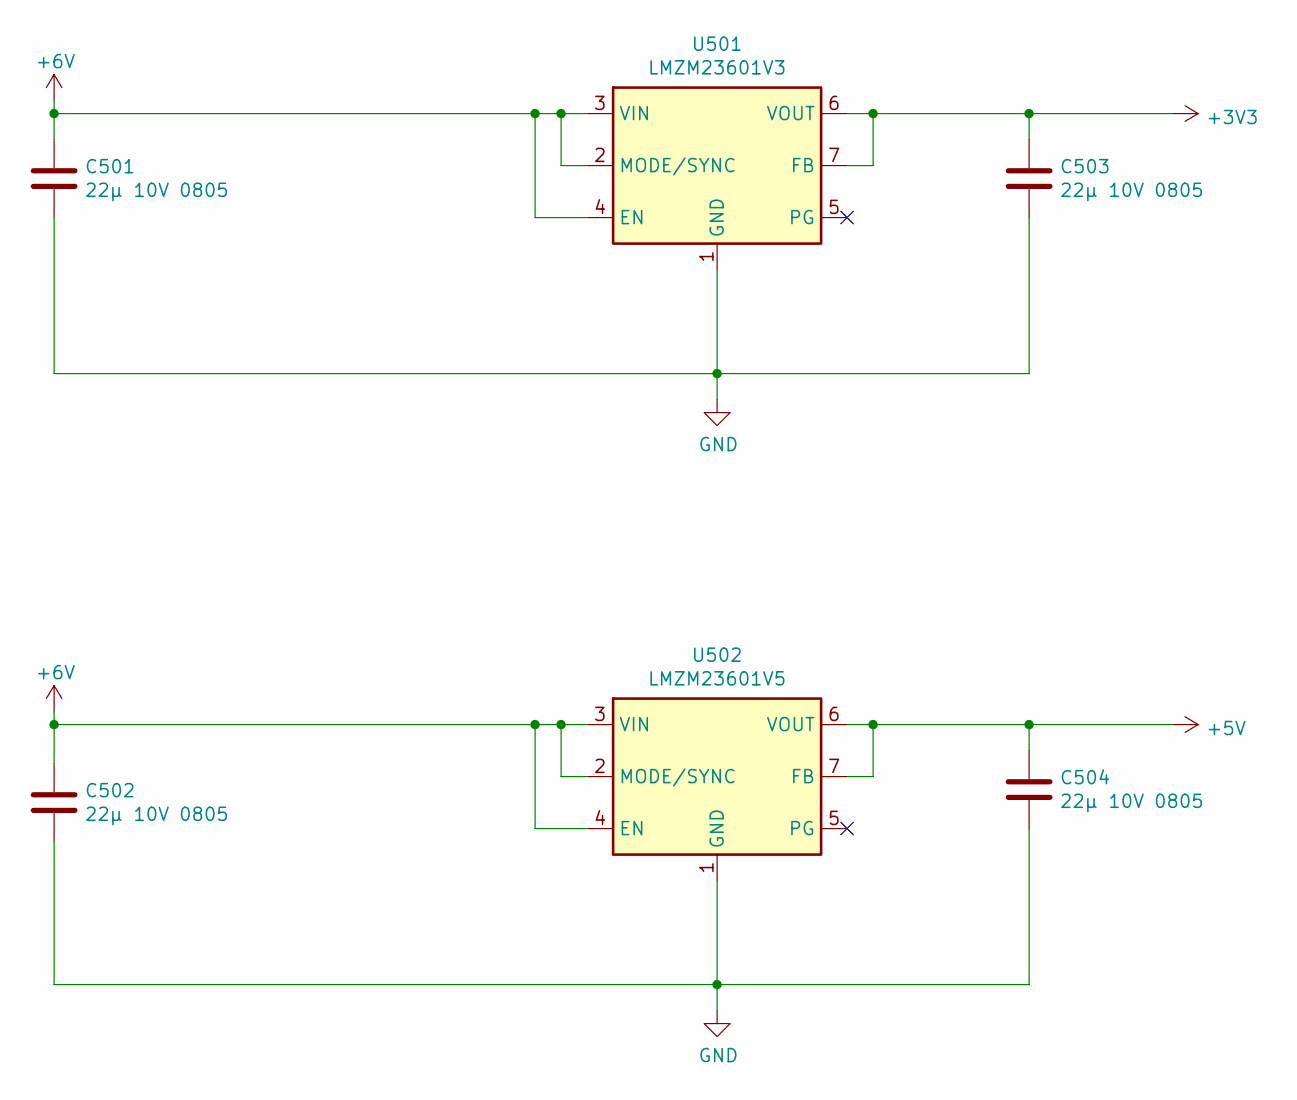
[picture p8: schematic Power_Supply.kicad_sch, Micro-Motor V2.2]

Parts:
C501, C502, C503, C504: 22µ 10V 0805; C_0805_2012Metric
U501: LMZM23601V3; Texas_SIL0010A_MicroSiP-10-1EP_3.8x3mm_P0.6mm_EP0.7x2.9mm
U502: LMZM23601V5; Texas_SIL0010A_MicroSiP-10-1EP_3.8x3mm_P0.6mm_EP0.7x2.9mm

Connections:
+3V3: C503.1, U501.6 (VOUT), U501.7 (FB); also elsewhere on the board
+5V: C504.1, U502.6 (VOUT), U502.7 (FB); also elsewhere on the board
+6V: C501.1, C502.1, U501.2 (MODE/SYNC), U501.3 (VIN), U501.4 (EN), U502.2 (MODE/SYNC), U502.3 (VIN), U502.4 (EN); also elsewhere on the board
GND: C501.2, C502.2, C503.2, C504.2, U501.1 (GND), U501.11 (GND), U502.1 (GND), U502.11 (GND); also elsewhere on the board

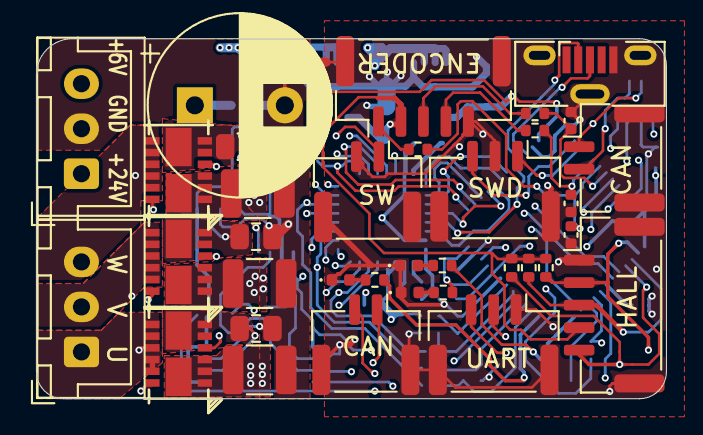
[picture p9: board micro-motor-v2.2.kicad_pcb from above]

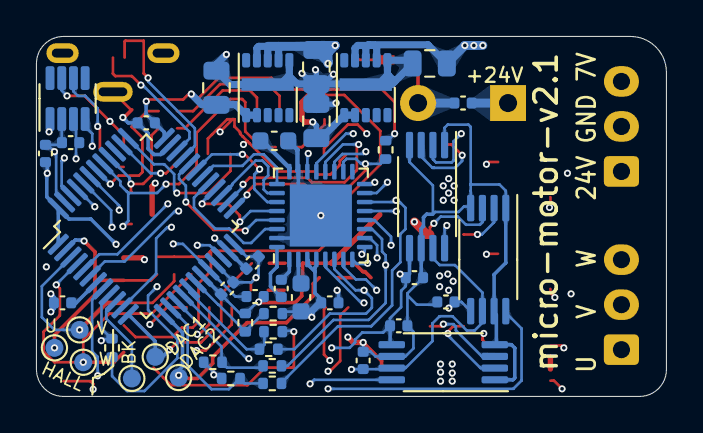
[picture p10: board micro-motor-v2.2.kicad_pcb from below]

Board: 4 copper layers, 35.0 x 20.0 mm, 80 parts (44 on the bottom side), 68 nets.

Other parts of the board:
J107: CAN; JST_GH_BM02B-GHS-TBT_1x02-1MP_P1.25mm_Vertical

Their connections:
/Can/CANH: J107.1; also elsewhere on the board
/Can/CANL: J107.2; also elsewhere on the board
GND: J107.MP (MountPin); also elsewhere on the board

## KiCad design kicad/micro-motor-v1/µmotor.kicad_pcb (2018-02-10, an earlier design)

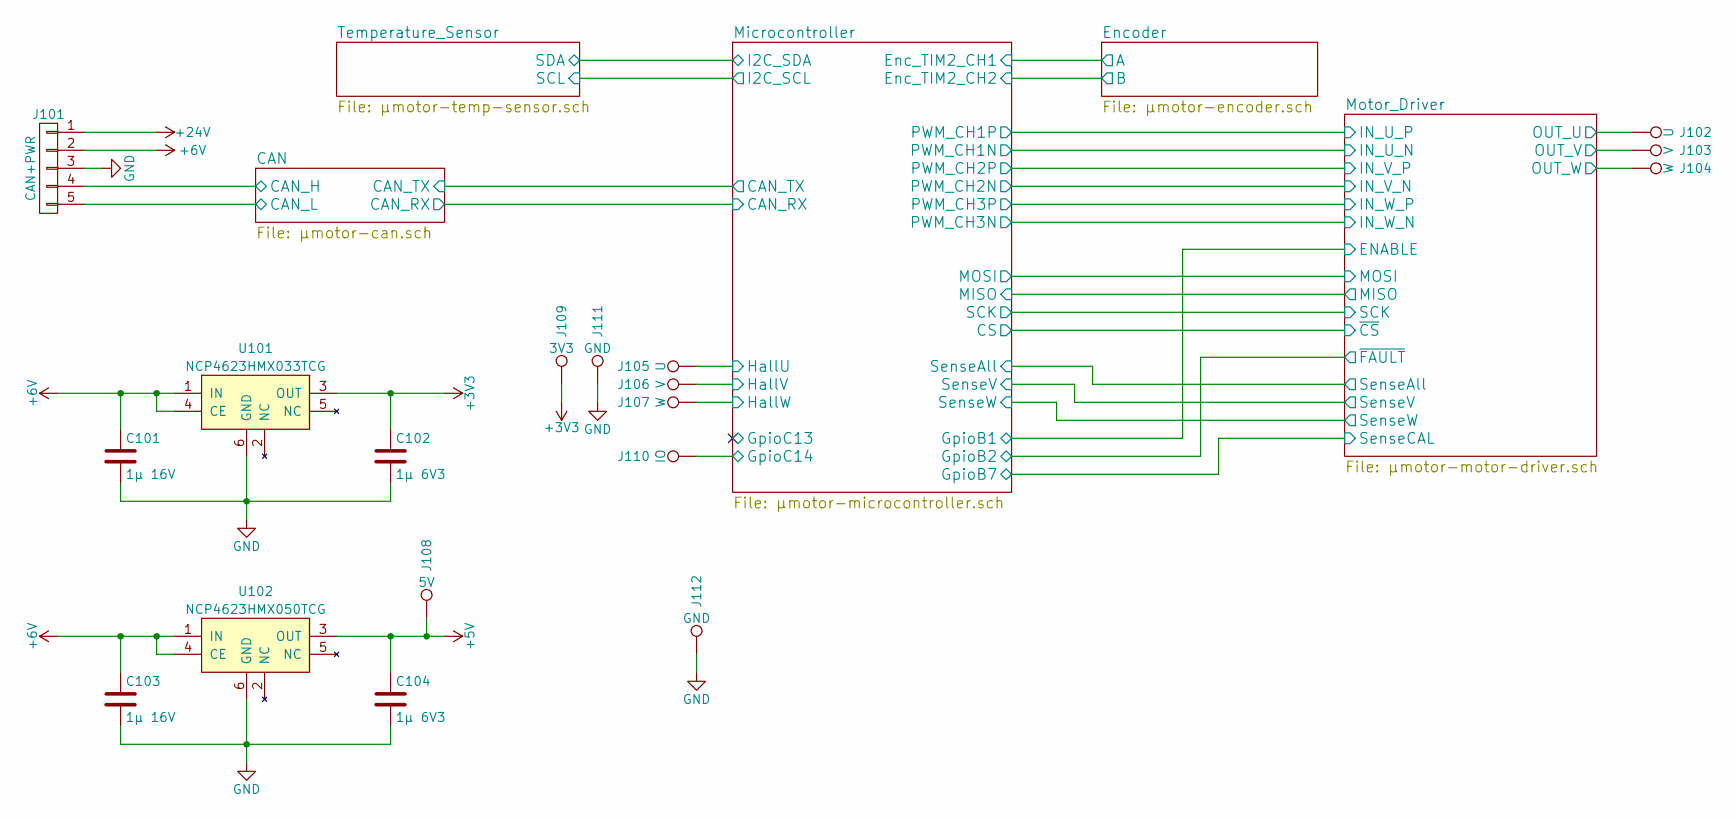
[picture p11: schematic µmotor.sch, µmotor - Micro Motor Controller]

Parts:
C101, C103: 1µ 16V; C_0603
C102, C104: 1µ 6V3; C_0603
J101: CAN+PWR; Pin_Header_Straight_1x05_Pitch2.54mm
J102: U; Measurement_Point_Round-TH_Small
J103: V; Measurement_Point_Round-TH_Small
J104: W; Measurement_Point_Round-TH_Small
J105: U; Measurement_Point_Round-SMD-Pad_Smaller_0.75mm
J106: V; Measurement_Point_Round-SMD-Pad_Smaller_0.75mm
J107: W; Measurement_Point_Round-SMD-Pad_Smaller_0.75mm
J108: 5V; Measurement_Point_Round-SMD-Pad_Smaller_0.75mm
J109: 3V3; Measurement_Point_Round-SMD-Pad_Smaller_0.75mm
J110: IO; Measurement_Point_Round-SMD-Pad_Smaller_0.75mm
J111, J112: GND; Measurement_Point_Round-SMD-Pad_Smaller_0.75mm
U101: NCP4623HMX033TCG; DFN-6-1EP_2x2mm_Pitch0.5mm
U102: NCP4623HMX050TCG; DFN-6-1EP_2x2mm_Pitch0.5mm

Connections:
+3V3: C102.1, J109.1, U101.3 (OUT); also elsewhere on the board
+5V: C104.1, J108.1, U102.3 (OUT)
+6V: C101.1, C103.1, J101.2, U101.1 (IN), U101.4 (CE), U102.1 (IN), U102.4 (CE); also elsewhere on the board
+24V: J101.1; also elsewhere on the board
/CAN/CAN_H: J101.4; also elsewhere on the board
/CAN/CAN_L: J101.5; also elsewhere on the board
/Microcontroller/GpioC14: J110.1; also elsewhere on the board
/Microcontroller/HallU: J105.1; also elsewhere on the board
/Microcontroller/HallV: J106.1; also elsewhere on the board
/Microcontroller/HallW: J107.1; also elsewhere on the board
/Motor_Driver/OUT_U: J102.1; also elsewhere on the board
/Motor_Driver/OUT_V: J103.1; also elsewhere on the board
/Motor_Driver/OUT_W: J104.1; also elsewhere on the board
GND: C101.2, C102.2, C103.2, C104.2, J101.3, J111.1, J112.1, U101.6 (GND), U101.7 (GND), U102.6 (GND), U102.7 (GND); also elsewhere on the board

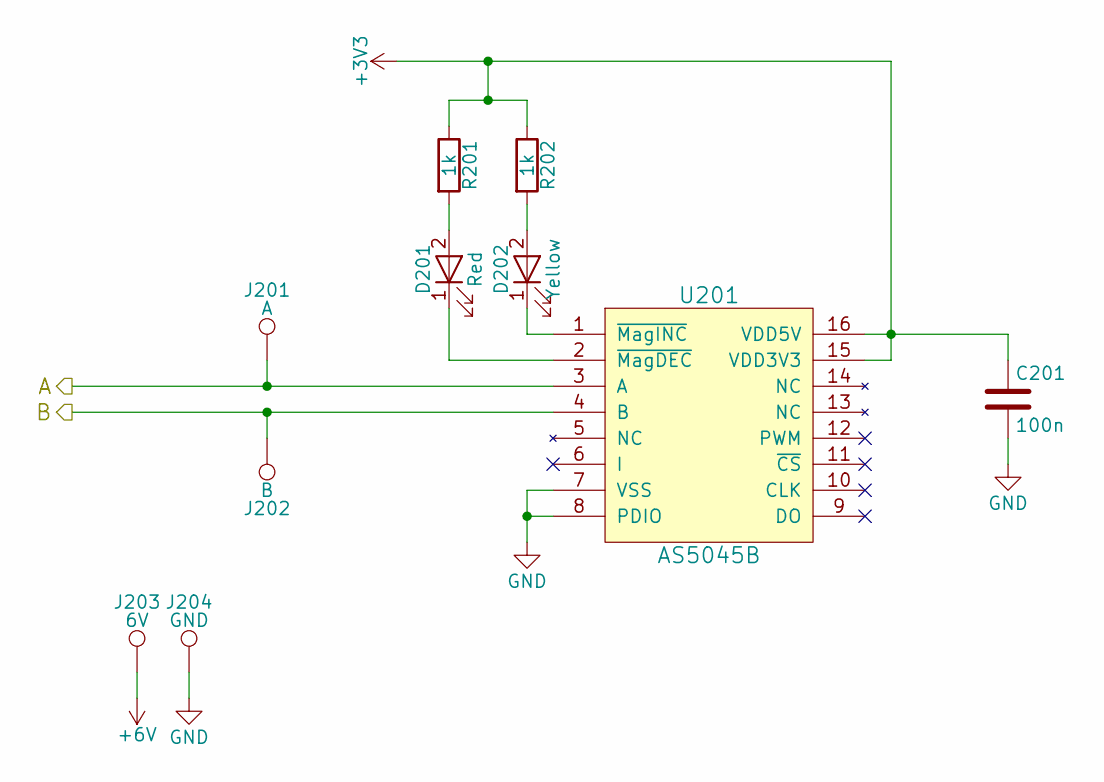
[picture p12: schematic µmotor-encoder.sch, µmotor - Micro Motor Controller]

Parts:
C201: 100n; C_0603
D201: Red; LED_0603
D202: Yellow; LED_0603
J201: A; Measurement_Point_Round-SMD-Pad_Smaller_0.75mm
J202: B; Measurement_Point_Round-SMD-Pad_Smaller_0.75mm
J203: 6V; Measurement_Point_Round-SMD-Pad_Smaller_0.75mm
J204: GND; Measurement_Point_Round-SMD-Pad_Smaller_0.75mm
R201, R202: 1k; R_0603
U201: AS5045B; SSOP-16_4.4x5.2mm_Pitch0.65mm

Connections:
+3V3: C201.1, R201.1, R202.1, U201.15 (VDD3V3), U201.16 (VDD5V); also elsewhere on the board
+6V: J203.1; also elsewhere on the board
/Encoder/A: J201.1, U201.3 (A); also elsewhere on the board
/Encoder/B: J202.1, U201.4 (B); also elsewhere on the board
GND: C201.2, J204.1, U201.7 (VSS), U201.8 (PDIO); also elsewhere on the board
unnamed: D201.1 (K), U201.2 (~MagDEC)
unnamed: D201.2 (A), R201.2
unnamed: D202.1 (K), U201.1 (~MagINC)
unnamed: D202.2 (A), R202.2

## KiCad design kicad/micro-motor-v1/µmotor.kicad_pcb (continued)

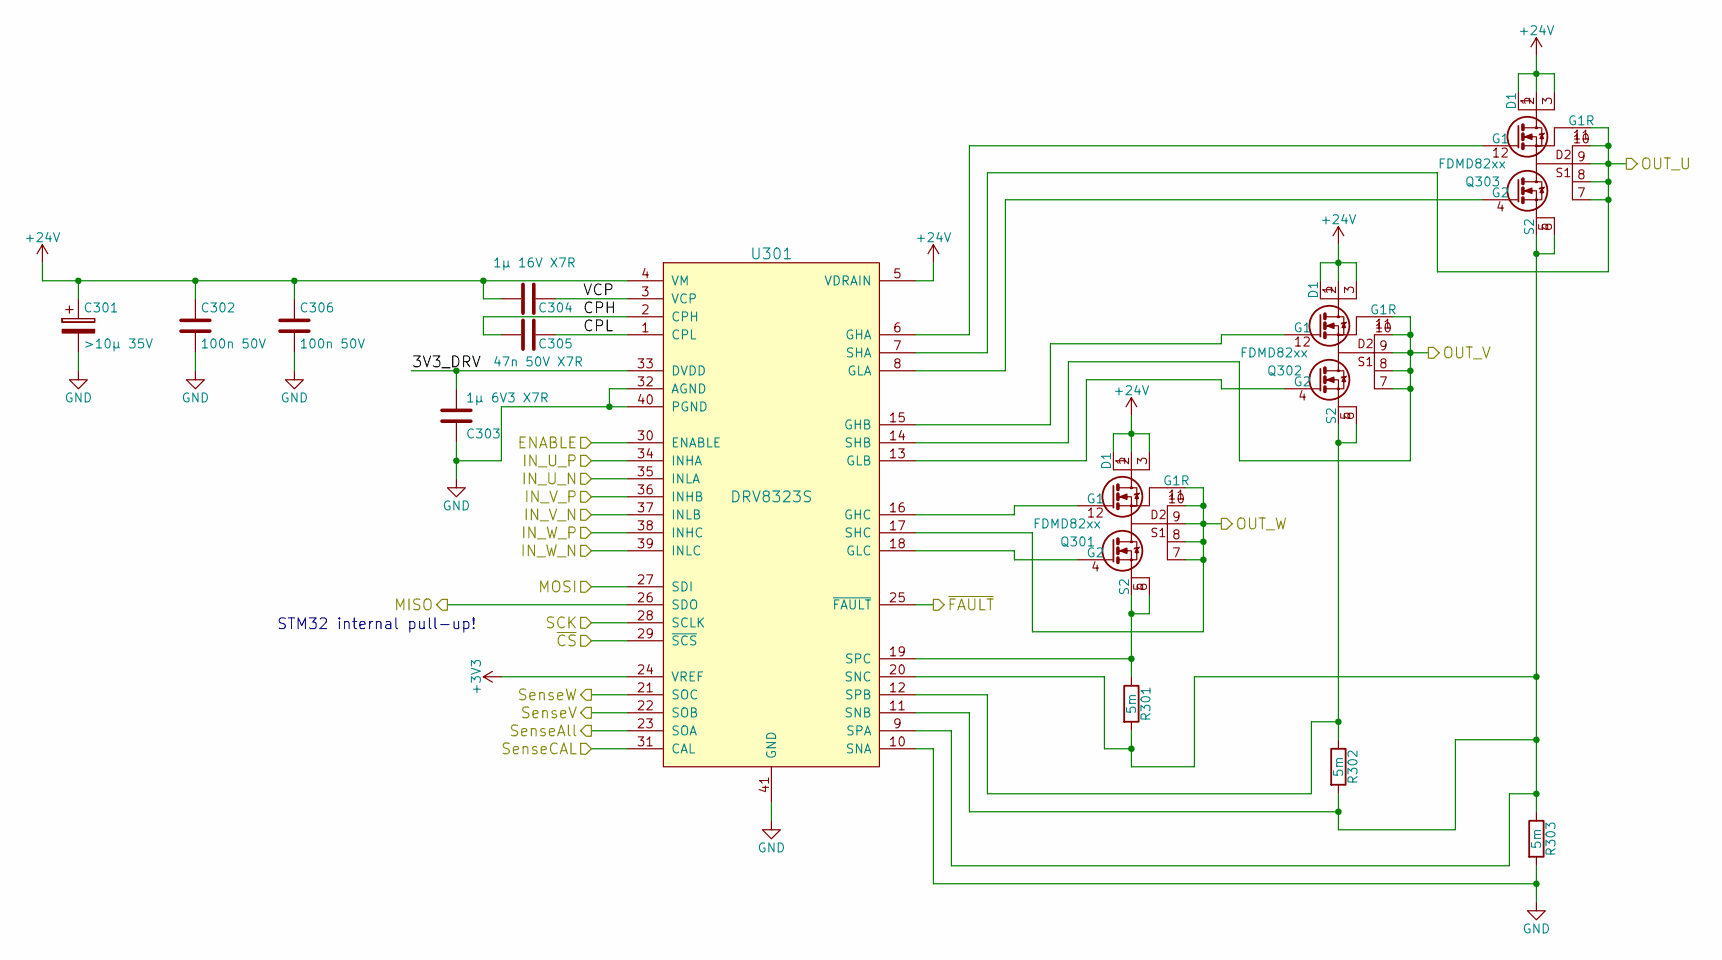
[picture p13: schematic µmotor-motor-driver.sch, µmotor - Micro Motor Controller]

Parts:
C301: >10µ 35V; CP_Radial_D4.0mm_P2.00mm
C302, C306: 100n 50V; C_0603
C303: 1µ 6V3 X7R; C_0603
C304: 1µ 16V X7R; C_0603
C305: 47n 50V X7R; C_0603
Q301, Q302, Q303: FDMD82xx; DFN-12-2EP_3.3x5mm_Pitch0.65mm
R301, R302, R303: 5m; R_0805
U301: DRV8323S; QFN-40-1EP_6x6mm_Pitch0.5mm

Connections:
+3V3: U301.24 (VREF); also elsewhere on the board
+24V: C301.1, C302.1, C304.2, C306.1, Q301.1 (D1), Q301.2, Q301.3, Q301.13 (D1), Q302.1 (D1), Q302.2, Q302.3, Q302.13 (D1), Q303.1 (D1), Q303.2, Q303.3, Q303.13 (D1), U301.4 (VM), U301.5 (VDRAIN); also elsewhere on the board
/Microcontroller/CS: U301.29 (~SCS); also elsewhere on the board
/Microcontroller/GpioB2: U301.25 (~FAULT); also elsewhere on the board
/Microcontroller/GpioB7: U301.31 (CAL); also elsewhere on the board
/Microcontroller/MISO: U301.26 (SDO); also elsewhere on the board
/Microcontroller/MOSI: U301.27 (SDI); also elsewhere on the board
/Microcontroller/SCK: U301.28 (SCLK); also elsewhere on the board
/Microcontroller/SenseAll: U301.23 (SOA); also elsewhere on the board
/Microcontroller/SenseV: U301.22 (SOB); also elsewhere on the board
/Microcontroller/SenseW: U301.21 (SOC); also elsewhere on the board
/Motor_Driver/3V3_DRV: C303.1, U301.33 (DVDD)
/Motor_Driver/CPH: C305.2, U301.2 (CPH)
/Motor_Driver/CPL: C305.1, U301.1 (CPL)
/Motor_Driver/ENABLE: U301.30 (ENABLE); also elsewhere on the board
/Motor_Driver/IN_U_N: U301.35 (INLA); also elsewhere on the board
/Motor_Driver/IN_U_P: U301.34 (INHA); also elsewhere on the board
/Motor_Driver/IN_V_N: U301.37 (INLB); also elsewhere on the board
/Motor_Driver/IN_V_P: U301.36 (INHB); also elsewhere on the board
/Motor_Driver/IN_W_N: U301.39 (INLC); also elsewhere on the board
/Motor_Driver/IN_W_P: U301.38 (INHC); also elsewhere on the board
/Motor_Driver/OUT_U: Q303.7, Q303.8, Q303.9, Q303.10, Q303.11 (G1R), U301.7 (SHA); also elsewhere on the board
/Motor_Driver/OUT_V: Q302.7, Q302.8, Q302.9, Q302.10, Q302.11 (G1R), U301.14 (SHB); also elsewhere on the board
/Motor_Driver/OUT_W: Q301.7, Q301.8, Q301.9, Q301.10, Q301.11 (G1R), U301.17 (SHC); also elsewhere on the board
/Motor_Driver/VCP: C304.1, U301.3 (VCP)
GND: C301.2, C302.2, C303.2, C306.2, R303.2, U301.10 (SNA), U301.32 (AGND), U301.40 (PGND), U301.41 (GND); also elsewhere on the board
unnamed: Q301.4 (G2), U301.18 (GLC)
unnamed: Q301.12 (G1), U301.16 (GHC)
unnamed: Q301.5 (S2), Q301.6, Q301.14 (S2), R301.1, U301.19 (SPC)
unnamed: Q302.4 (G2), U301.13 (GLB)
unnamed: Q302.12 (G1), U301.15 (GHB)
unnamed: Q302.5 (S2), Q302.6, Q302.14 (S2), R302.1, U301.12 (SPB)
unnamed: Q303.4 (G2), U301.8 (GLA)
unnamed: Q303.12 (G1), U301.6 (GHA)
unnamed: Q303.5 (S2), Q303.6, Q303.14 (S2), R301.2, R302.2, R303.1, U301.9 (SPA), U301.11 (SNB), U301.20 (SNC)

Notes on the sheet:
STM32 internal pull-up!

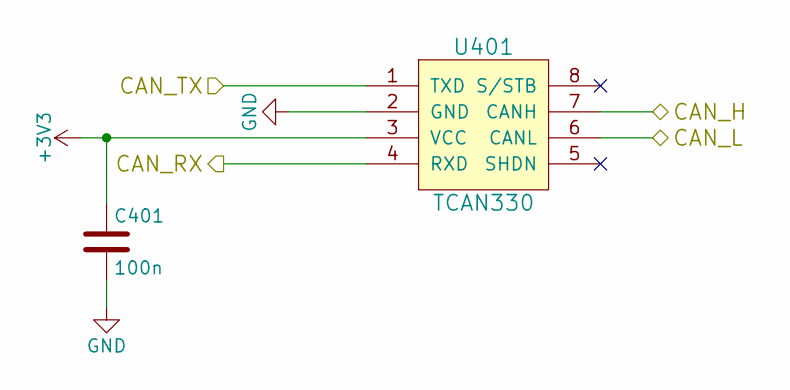
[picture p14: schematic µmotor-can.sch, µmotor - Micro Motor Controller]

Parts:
C401: 100n; C_0603
U401: TCAN330; SOT-23-8

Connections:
+3V3: C401.1, U401.3 (VCC); also elsewhere on the board
/CAN/CAN_H: U401.7 (CANH); also elsewhere on the board
/CAN/CAN_L: U401.6 (CANL); also elsewhere on the board
/CAN/CAN_RX: U401.4 (RXD); also elsewhere on the board
/CAN/CAN_TX: U401.1 (TXD); also elsewhere on the board
GND: C401.2, U401.2 (GND); also elsewhere on the board


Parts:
J501: SCL; Measurement_Point_Round-SMD-Pad_Smaller_0.75mm
J502: SDA; Measurement_Point_Round-SMD-Pad_Smaller_0.75mm
J503: 3V3; Measurement_Point_Round-SMD-Pad_Smaller_0.75mm
J504: GND; Measurement_Point_Round-SMD-Pad_Smaller_0.75mm
U501: TMP006; WCSP-8_1.6x1.6mm_P0.5mm

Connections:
+3V3: J503.1, U501.A3 (V+); also elsewhere on the board
/Microcontroller/I2C_SCL: J501.1, U501.B3 (SCL); also elsewhere on the board
/Microcontroller/I2C_SDA: J502.1, U501.C3 (SDA); also elsewhere on the board
GND: J504.1, U501.A1 (DGND), U501.A2 (AGND), U501.B1 (ADR1), U501.C1 (ADR0); also elsewhere on the board


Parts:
C601, C602: 100n; C_0603
C603: C; C_0402
D601: Blue; LED_0603
D602: Red; LED_0603
J601: GND; Measurement_Point_Round-SMD-Pad_Smaller_0.75mm
J602: SWCLK; Measurement_Point_Round-SMD-Pad_Smaller_0.5mm
J603: SWDIO; Measurement_Point_Round-SMD-Pad_Smaller_0.5mm
J604: TX; Measurement_Point_Round-SMD-Pad_Smaller_0.5mm
R601, R602: 1k; R_0603
TP602: BK; Measurement_Point_Round-SMD-Pad_Smaller_0.5mm
TP603: DAC; Measurement_Point_Round-SMD-Pad_Smaller_0.5mm
U601: STM32L433C(B-C)Ux_u; QFN-48-1EP_7x7mm_Pitch0.5mm

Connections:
+3V3: C601.1, C602.1, D601.2 (A), D602.2 (A), U601.1 (VBAT), U601.9 (VDDA/VREF+), U601.24 (VDD), U601.36 (VDDUSB), U601.48 (VDD); also elsewhere on the board
/CAN/CAN_RX: U601.32 (PA11/ADC1_EXTI11/CAN1_RX/COMP1_OUT/SPI1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); also elsewhere on the board
/CAN/CAN_TX: U601.33 (PA12/CAN1_TX/SPI1_MOSI/TIM1_ETR/USART1_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); also elsewhere on the board
/Encoder/A: U601.10 (PA0/ADC1_IN5/COMP1_INM/COMP1_OUT/OPAMP1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); also elsewhere on the board
/Encoder/B: U601.11 (PA1/ADC1_IN6/COMP1_INP/I2C1_SMBA/LCD_SE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); also elsewhere on the board
/Microcontroller/BK: TP602.1, U601.17 (PA7/ADC1_IN12/COMP2_OUT/I2C3_SCL/LCD_SE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)
/Microcontroller/CS: U601.38 (PA15(JTDI)/ADC1_EXTI15/LCD_SEG17/SPI1_N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); also elsewhere on the board
/Microcontroller/DAC: TP603.1, U601.15 (PA5/ADC1_IN10/COMP1_INM/COMP2_INM/DAC1_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)
/Microcontroller/GpioB2: U601.20 (PB2/COMP1_INP/I2C3_SMBA/LCD_VLCD/LPTIM1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); also elsewhere on the board
/Microcontroller/GpioB7: U601.43 (PB7/COMP2_INM/I2C1_SDA/LCD_SEG21/LPTIM1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); also elsewhere on the board
/Microcontroller/GpioC14: U601.3 (PC14-OSC32_IN(PC14)/RCC_OSC32_IN); also elsewhere on the board
/Microcontroller/HallU: U601.46 (PB9/CAN1_TX/DAC1_EXTI9/I2C1_SDA/IR_OUT/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); also elsewhere on the board
/Microcontroller/HallV: U601.45 (PB8/CAN1_RX/I2C1_SCL/LCD_SEG16/SAI1_MCL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); also elsewhere on the board
/Microcontroller/HallW: U601.42 (PB6/COMP2_INP/I2C1_SCL/LPTIM1_ETR/SAI1_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); also elsewhere on the board
/Microcontroller/I2C_SCL: U601.21 (PB10/COMP1_OUT/I2C2_SCL/LCD_SEG10/LPUAR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); also elsewhere on the board
/Microcontroller/I2C_SDA: U601.22 (PB11/ADC1_EXTI11/COMP2_OUT/I2C2_SDA/LCD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); also elsewhere on the board
/Microcontroller/LedBlue: R601.1, U601.25 (PB12/I2C2_SMBA/LCD_SEG12/LPUART1_DE/LPU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)
/Microcontroller/LedBlueR: D601.1 (K), R601.2
/Microcontroller/LedRed: R602.1, U601.5 (PH0-OSC_IN(PH0)/RCC_OSC_IN)
/Microcontroller/LedRedR: D602.1 (K), R602.2
/Microcontroller/MISO: U601.40 (PB4(NJTRST)/COMP2_INP/I2C3_SDA/LCD_SEG8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); also elsewhere on the board
/Microcontroller/MOSI: U601.41 (PB5/COMP2_OUT/I2C1_SMBA/LCD_SEG9/LPTIM1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); also elsewhere on the board
/Microcontroller/SCK: U601.39 (PB3(JTDO-TRACESWO)/COMP2_INM/LCD_SEG7/S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); also elsewhere on the board
/Microcontroller/SWCLK: J602.1, U601.37 (PA14(JTCK-SWCLK)/I2C1_SMBA/LPTIM1_OUT/S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)
/Microcontroller/SWDIO: J603.1, U601.34 (PA13(JTMS-SWDIO)/IR_OUT/SAI1_SD_B/SWPMI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)
/Microcontroller/SenseAll: U601.13 (PA3/ADC1_IN8/COMP2_INP/LCD_SEG2/LPUART1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), U601.14 (PA4/ADC1_IN9/COMP1_INM/COMP2_INM/DAC1_O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); also elsewhere on the board
/Microcontroller/SenseV: U601.16 (PA6/ADC1_IN11/COMP1_OUT/LCD_SEG3/LPUART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); also elsewhere on the board
/Microcontroller/SenseW: U601.18 (PB0/ADC1_IN15/COMP1_OUT/LCD_SEG5/QUADSP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); also elsewhere on the board
/Microcontroller/TX: J604.1, U601.12 (PA2/ADC1_IN7/COMP2_INM/COMP2_OUT/LCD_SE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)
/Microcontroller/~RST: C603.1, U601.7 (NRST)
/Motor_Driver/ENABLE: U601.19 (PB1/ADC1_IN16/COMP1_INM/LCD_SEG6/LPTIM2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); also elsewhere on the board
/Motor_Driver/IN_U_N: U601.26 (PB13/I2C2_SCL/LCD_SEG13/LPUART1_CTS/SAI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); also elsewhere on the board
/Motor_Driver/IN_U_P: U601.29 (PA8/LCD_COM0/LPTIM2_OUT/RCC_MCO/SAI1_SC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); also elsewhere on the board
/Motor_Driver/IN_V_N: U601.27 (PB14/I2C2_SDA/LCD_SEG14/SAI1_MCLK_A/SPI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); also elsewhere on the board
/Motor_Driver/IN_V_P: U601.30 (PA9/DAC1_EXTI9/I2C1_SCL/LCD_COM1/SAI1_F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); also elsewhere on the board
/Motor_Driver/IN_W_N: U601.28 (PB15/ADC1_EXTI15/LCD_SEG15/RTC_REFIN/SA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); also elsewhere on the board
/Motor_Driver/IN_W_P: U601.31 (PA10/CRS_SYNC/I2C1_SDA/LCD_COM2/SAI1_SD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); also elsewhere on the board
GND: C601.2, C602.2, C603.2, J601.1, U601.8 (VSSA/VREF-), U601.23 (VSS), U601.35 (VSS), U601.44 (PH3-BOOT0), U601.47 (VSS), U601.49 (Pad); also elsewhere on the board

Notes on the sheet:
SWD
UART
Debug LED



Board: 4 copper layers, 20.0 x 20.0 mm, 62 parts (32 on the bottom side), 63 nets.

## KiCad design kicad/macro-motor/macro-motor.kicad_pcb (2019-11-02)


Board: 2 copper layers, 100.0 x 35.0 mm, 116 parts (1 on the bottom side), 74 nets.

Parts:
C101: 4µ7 16V; C_0603_1608Metric
C102, C103: 2µ2 6V3; C_0402_1005Metric
C201, C206, C401, C501, C601, C602, C603: 100n; C_0402_1005Metric
C202, C203, C204, C205: (2n7); C_0402_1005Metric
C301: >10µ 35V; CP_Radial_D8.0mm_P3.50mm
C302: 100n 50V; C_0603_1608Metric
C303: 100n 50V; C_0402_1005Metric
C304: 1µ 6V3 X7R; C_0402_1005Metric
C305: 1µ 16V X7R; C_0402_1005Metric
C306: 47n 50V X7R; C_0402_1005Metric
D601: Blue; LED_0402_1005Metric
D602: Red; LED_0402_1005Metric
J101: CAN+PWR; PinHeader_1x05_P2.54mm_Vertical
J102, J503: 3V3; Pin_D1.0mm_L10.0mm
J103: 5V; Pin_D1.0mm_L10.0mm
J104, J504: GND; Pin_D1.0mm_L10.0mm
J105: Gpio; Pin_D1.0mm_L10.0mm
J106: U; Pin_D1.0mm_L10.0mm
J107: V; Pin_D1.0mm_L10.0mm
J108: W; Pin_D1.0mm_L10.0mm
J109: Conn_01x03_Female; TerminalBlock_Phoenix_PT-1,5-3-3.5-H_1x03_P3.50mm_Horizontal
J110: HALL; PinHeader_1x05_P2.54mm_Vertical
J111: Fault; Pin_D1.0mm_L10.0mm
J202: B; Pin_D1.0mm_L10.0mm
J203: A; Pin_D1.0mm_L10.0mm
J204: Encoder; PinHeader_1x06_P2.54mm_Vertical
J301: A; PinHeader_1x02_P2.54mm_Vertical
J302: B; PinHeader_1x02_P2.54mm_Vertical
J303: C; PinHeader_1x02_P2.54mm_Vertical
J501: SCL; Pin_D1.0mm_L10.0mm
J502: SDA; Pin_D1.0mm_L10.0mm
J601: SWD; PinHeader_1x03_P2.54mm_Vertical
J604: UART; PinHeader_1x03_P2.54mm_Vertical
J605: OP_INM; Pin_D1.0mm_L10.0mm
J606: OP_OUT; Pin_D1.0mm_L10.0mm
J607: PA0; Pin_D1.0mm_L10.0mm
J608: PH1; Pin_D1.0mm_L10.0mm
J609: PH0; Pin_D1.0mm_L10.0mm
JP301: SPC; SolderJumper-2_P1.3mm_Open_RoundedPad1.0x1.5mm
JP302: SPB; SolderJumper-2_P1.3mm_Open_RoundedPad1.0x1.5mm
JP303: SPA; SolderJumper-2_P1.3mm_Open_RoundedPad1.0x1.5mm
Q301, Q302, Q303: FDMD82xx; DFN-12-2EP_3.3x5mm_Pitch0.65mm
R101, R301, R603, R605, R606, R607, R608: 10k; R_0402_1005Metric
R102, R103, R104, R601, R602, R604: 1k; R_0402_1005Metric
R105, R106, R107: 20k; R_0402_1005Metric
R108: (10k); R_0402_1005Metric
R203, R204, R205, R206: 47k; R_0402_1005Metric
R302, R303, R304: 5m; R_0805_2012Metric
R501, R502: 4k7; R_0402_1005Metric
RN201: (2k7); EXB18V
RN202: (100); EXB18V
TP301: +24V; Pin_D1.0mm_L10.0mm
TP302: GND; Pin_D1.0mm_L10.0mm
TP303, TP304: UP; Pin_D1.0mm_L10.0mm
TP305: VP; Pin_D1.0mm_L10.0mm
TP306: VN; Pin_D1.0mm_L10.0mm
TP307: WP; Pin_D1.0mm_L10.0mm
TP308: WN; Pin_D1.0mm_L10.0mm
TP309: MOSI; Pin_D1.0mm_L10.0mm
TP310: MISO; Pin_D1.0mm_L10.0mm
TP311: SCK; Pin_D1.0mm_L10.0mm
TP312: ~CS; Pin_D1.0mm_L10.0mm
TP313, TP322: W; Pin_D1.0mm_L10.0mm
TP314, TP323: V; Pin_D1.0mm_L10.0mm
TP315, TP324: U; Pin_D1.0mm_L10.0mm
TP316: GH_U; Pin_D1.0mm_L10.0mm
TP317: GL_U; Pin_D1.0mm_L10.0mm
TP318: GH_W; Pin_D1.0mm_L10.0mm
TP319: GL_W; Pin_D1.0mm_L10.0mm
TP320: GH_V; Pin_D1.0mm_L10.0mm
TP321: GL_V; Pin_D1.0mm_L10.0mm
U101: ADP7112ACBZ-3.3-R7; WLCSP-6_1.4x1.0mm_P0.4mm
U102: ADP7112ACBZ-5.0-R7; WLCSP-6_1.4x1.0mm_P0.4mm
U201, U202: ISL3280E; SOT-23-5
U301: DRV8323S; QFN-40-1EP_6x6mm_P0.5mm_EP4.6x4.6mm
U401: TCAN330; SOT-23-8
U501: TMP006; WCSP-8_1.6x1.6mm_P0.5mm
U601: STM32L433C(B-C)Ux_u; QFN-48-1EP_7x7mm_P0.5mm_EP5.6x5.6mm

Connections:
+3V3: C102.1, C201.1, C206.1, C401.1, C501.1, C602.1, C603.1, J102.1, J503.1, R101.2, R108.1, R301.2, R501.1, R502.1, R601.2, U101.A2, U101.B2, U201.1, U202.1, U301.24, U401.3, U501.A3, U601.1, U601.9, U601.24, U601.36, U601.48
+5V: C103.1, J103.1, J110.4, J204.4, R203.1, R205.1, RN201.1, RN201.2, RN201.3, RN201.4, U102.A2, U102.B2
+6V: C101.1, J101.4, U101.A1, U101.C1, U102.A1, U102.C1
+24V: C301.1, C302.1, C303.1, C305.2, J101.5, Q301.1, Q301.2, Q301.3, Q301.13, Q302.1, Q302.2, Q302.3, Q302.13, Q303.1, Q303.2, Q303.3, Q303.13, R603.2, TP301.1, U301.4, U301.5
/CAN/CAN_H: J101.2, U401.7
/CAN/CAN_L: J101.1, U401.6
/CAN/CAN_RX: U401.4, U601.45
/CAN/CAN_TX: U401.1, U601.46
/Encoder/A: J203.1, U202.3, U601.38
/Encoder/B: J202.1, U201.3, U601.39
/Microcontroller/BemfU: R104.1, R105.2, U601.17
/Microcontroller/BemfV: R103.1, R106.2, U601.18
/Microcontroller/BemfW: R102.1, R107.2, U601.19
/Microcontroller/CS: TP312.1, U301.29, U601.33
/Microcontroller/CurrentU: R605.2, TP315.1, U301.23, U601.14
/Microcontroller/CurrentV: R606.2, TP314.1, U301.22, U601.15
/Microcontroller/CurrentW: R607.2, TP313.1, U301.21
/Microcontroller/Fault: J111.1, R108.2, U301.25, U601.40
/Microcontroller/Gpio: J105.1, R101.1, U601.20
/Microcontroller/HallU: J106.1, J110.2, U601.2
/Microcontroller/HallV: J107.1, J110.3, U601.3
/Microcontroller/HallW: J108.1, J110.5, U601.4
/Microcontroller/I2C_SCL: J501.1, R501.2, U501.B3, U601.21
/Microcontroller/I2C_SDA: J502.1, R502.2, U501.C3, U601.22
/Microcontroller/Led: D601.1, D602.2, U601.25
/Microcontroller/LedCom: D601.2, D602.1, R601.1, R602.2
/Microcontroller/MISO: R301.1, TP310.1, U301.26, U601.43
/Microcontroller/MOSI: TP309.1, U301.27, U601.42
/Microcontroller/OP_INM: J605.1, R605.1, R606.1, R607.1, R608.2, U601.11
/Microcontroller/OP_OUT: J606.1, R608.1, U601.13
/Microcontroller/PA0: J607.1, U601.10
/Microcontroller/PH0: J609.1, U601.5
/Microcontroller/PH1: J608.1, U601.6
/Microcontroller/SCK: TP311.1, U301.28, U601.41
/Microcontroller/SWCLK: J601.1, U601.37
/Microcontroller/SWDIO: J601.3, U601.34
/Microcontroller/TX: J604.3, U601.12
/Microcontroller/~RST: C601.1, U601.7
/Motor_Driver/3V3_DRV: C304.2, U301.33
/Motor_Driver/CPH: C306.2, U301.2
/Motor_Driver/CPL: C306.1, U301.1
/Motor_Driver/ENABLE: U301.30, U601.32
/Motor_Driver/GH_U: Q303.12, TP316.1, U301.6
/Motor_Driver/GH_V: Q302.12, TP320.1, U301.15
/Motor_Driver/GH_W: Q301.12, TP318.1, U301.16
/Motor_Driver/GL_U: Q303.4, TP317.1, U301.8
/Motor_Driver/GL_V: Q302.4, TP321.1, U301.13
/Motor_Driver/GL_W: Q301.4, TP319.1, U301.18
/Motor_Driver/IN_U_N: TP304.1, U301.35, U601.26
/Motor_Driver/IN_U_P: TP303.1, U301.34, U601.29
/Motor_Driver/IN_V_N: TP306.1, U301.37, U601.27
/Motor_Driver/IN_V_P: TP305.1, U301.36, U601.30
/Motor_Driver/IN_W_N: TP308.1, U301.39, U601.28
/Motor_Driver/IN_W_P: TP307.1, U301.38, U601.31
/Motor_Driver/OUT_U: J109.1, Q303.7, Q303.8, Q303.9, Q303.10, Q303.11, R105.1, TP324.1, U301.7
/Motor_Driver/OUT_V: J109.2, Q302.7, Q302.8, Q302.9, Q302.10, Q302.11, R106.1, TP323.1, U301.14
/Motor_Driver/OUT_W: J109.3, Q301.7, Q301.8, Q301.9, Q301.10, Q301.11, R107.1, TP322.1, U301.17
/Motor_Driver/VCP: C305.1, U301.3
GND: C101.2, C102.2, C103.2, C201.2, C202.1, C203.1, C204.1, C205.1, C206.2, C301.2, C302.2, C303.2, C304.1, C401.2, C501.2, C601.2, C602.2, C603.2, J101.3, J104.1, J110.1, J204.3, J303.2, J504.1, J601.2, J604.1, R102.2, R103.2, R104.2, R204.2, R206.2, R304.2, R602.1, R604.1, TP302.1, U101.C2, U102.C2, U201.2, U202.2, U301.10, U301.31, U301.32, U301.40, U301.41, U401.2, U501.A1, U501.A2, U501.B1, U501.C1, U601.8, U601.23, U601.35, U601.44, U601.47, U601.49
unnamed: C202.2, RN202.5, U202.5
unnamed: C203.2, RN202.7, U201.5
unnamed: C204.2, RN202.6, U202.4
unnamed: C205.2, RN202.8, U201.4
unnamed: J204.1, R205.2, R206.1, RN201.6, RN202.3
unnamed: J204.2, RN201.5, RN202.4
unnamed: J204.5, RN201.7, RN202.2
unnamed: J204.6, R203.2, R204.1, RN201.8, RN202.1
unnamed: J301.1, JP301.2, Q301.5, Q301.6, Q301.14, R302.1
unnamed: J301.2, J302.2, J303.1, JP303.2, Q303.5, Q303.6, Q303.14, R302.2, R303.2, R304.1, U301.11, U301.20
unnamed: J302.1, JP302.2, Q302.5, Q302.6, Q302.14, R303.1
unnamed: JP301.1, U301.19
unnamed: JP302.1, U301.12
unnamed: JP303.1, U301.9
unnamed: R603.1, R604.2, U601.16

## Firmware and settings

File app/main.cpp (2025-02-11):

/* main.hpp
 *
 * Copyright (C) 2022-2023 Michael Jossen
 * Copyright (C) 2021-2022 Christopher Durand
 * Copyright (C) 2018 Raphael Lehmann <raphael@rleh.de>
 *
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
 * You should have received a copy of the GNU General Public License
 * along with this program.  If not, see <http://www.gnu.org/licenses/>.
 */

#include <micro-motor/micro-motor.hpp>
#include <modm/driver/motor/drv832x_spi.hpp>

#include <modm/debug/logger.hpp>
#include <modm/platform.hpp>
#include <modm/processing/timer.hpp>

#include <librobots2/motor-canopen/identity.hpp>
#include <micro-motor/canopen/canopen.hpp>
#include "motor.hpp"

#include <info_build.h>
#include <info_git.h>

inline modm::IODeviceWrapper<Board::Ui::DebugUart, modm::IOBuffer::BlockIfFull> loggerDevice;
inline modm::log::Logger modm::log::debug(loggerDevice);
inline modm::log::Logger modm::log::info(loggerDevice);
inline modm::log::Logger modm::log::warning(loggerDevice);
inline modm::log::Logger modm::log::error(loggerDevice);

using namespace std::literals;

modm::PeriodicTimer debugTimer{500ms};

modm::Drv832xSpi<Board::MotorBridge::GateDriver::Spi, Board::MotorBridge::GateDriver::Cs>
	gateDriver;

namespace
{

struct BoardId
{
	uint32_t id;
	uint32_t nodeId;
	uint8_t hw_version_major;
	uint8_t hw_version_minor;
};
uint8_t
readBoardId()
{
	static constexpr std::array boards = {
		// hardware id, board id
		BoardId{.id = 0x00320025u, .nodeId = 1u, .hw_version_major = 2, .hw_version_minor = 1},
		BoardId{.id = 0x0031002cu, .nodeId = 2u, .hw_version_major = 2, .hw_version_minor = 1},
		BoardId{.id = 0x00340045u, .nodeId = 3u, .hw_version_major = 2, .hw_version_minor = 1},
		BoardId{.id = 0x00340047u, .nodeId = 4u, .hw_version_major = 2, .hw_version_minor = 1},
		BoardId{.id = 0x002c0048u, .nodeId = 5u, .hw_version_major = 2, .hw_version_minor = 1},
		BoardId{.id = 0x002b0041u, .nodeId = 6u, .hw_version_major = 2, .hw_version_minor = 1},
		BoardId{.id = 0x002b0045u, .nodeId = 7u, .hw_version_major = 2, .hw_version_minor = 1},
		BoardId{.id = 0x002e002cu, .nodeId = 8u, .hw_version_major = 2, .hw_version_minor = 1},
		BoardId{.id = 0x002e002du, .nodeId = 9u, .hw_version_major = 2, .hw_version_minor = 1},
		BoardId{.id = 0x00320041u, .nodeId = 10u, .hw_version_major = 2, .hw_version_minor = 1},
		BoardId{.id = 0x002c004du, .nodeId = 11u, .hw_version_major = 2, .hw_version_minor = 1},
		BoardId{.id = 0x00390046u, .nodeId = 12u, .hw_version_major = 2, .hw_version_minor = 2},
		BoardId{.id = 0x00290044, .nodeId = 13u, .hw_version_major = 2, .hw_version_minor = 2},
		BoardId{.id = 0x002E0046, .nodeId = 14u, .hw_version_major = 2, .hw_version_minor = 2},
		BoardId{.id = 0x00410046, .nodeId = 15u, .hw_version_major = 2, .hw_version_minor = 2},
		BoardId{.id = 0x00320030, .nodeId = 17u, .hw_version_major = 2, .hw_version_minor = 2},
		BoardId{.id = 0x002C0050, .nodeId = 18u, .hw_version_major = 2, .hw_version_minor = 2},
	};

	const auto hardwareId = Board::readHardwareId();
	auto it = std::find_if(std::begin(boards), std::end(boards),
						   [hardwareId](auto board) { return board.id == hardwareId; });
	if (it == std::end(boards))
	{
		MODM_LOG_INFO << "Hardware ID: 0x" << modm::hex << hardwareId << modm::endl;
		MODM_LOG_ERROR << "Board not found" << modm::endl;
		Board::Ui::LedRed::set();
		while (1) asm volatile("nop");
	}
	if (it->hw_version_major != Board::Version_Major ||
		it->hw_version_minor != Board::Version_Minor)
	{
		MODM_LOG_INFO << "Hardware ID: 0x" << modm::hex << hardwareId << modm::endl;
		MODM_LOG_ERROR << "Wrong hardware version!" << modm::endl;
		MODM_LOG_ERROR << "Is v" << Board::Version_Major << "." << Board::Version_Minor
					   << modm::endl;
		MODM_LOG_ERROR << "Should be v" << it->hw_version_major << "." << it->hw_version_minor
					   << modm::endl;
		Board::Ui::LedRed::set();
		while (1) asm volatile("nop");
	}

	return it->nodeId;
}

}  // namespace

constexpr auto noMessageTimeout = 200ms;

constexpr modm_canopen::Identity micromotorId = {.deviceType_ = (uint32_t)DeviceType::BLDC,
												 .vendorId_ = 0xdeadbeef,
												 .productCode_ = (uint32_t)ProductCode::MicroMotor};

int
main()
{

	Board::initializeMcu();
	Board::initializeAllPeripherals();
	Board::Ui::initializeLeds();
	micro_motor::initialize();

	MODM_LOG_ERROR << "Micro-Motor Application controlling BLDC Motors via canOpen interace"
				   << modm::endl;
	MODM_LOG_INFO << "Compiled for board version v" << Board::Version_Major << "."
				  << Board::Version_Minor << modm::endl;

	// Let's print some information about the compiling host, user etc.
	MODM_LOG_INFO << "Machine:  " << MODM_BUILD_MACHINE << modm::endl;
	MODM_LOG_INFO << "User:     " << MODM_BUILD_USER << modm::endl;
	MODM_LOG_INFO << "Os:       " << MODM_BUILD_OS << modm::endl;
	MODM_LOG_INFO << "Compiler: " << MODM_BUILD_COMPILER << modm::endl;
	// Let's print some information about the git statud, that is provided in the
	// modm_git_info.hpp
	MODM_LOG_INFO << "Local Git User:" << modm::endl;
	MODM_LOG_INFO << "Name:  " << MODM_GIT_CONFIG_USER_NAME << "<" << MODM_GIT_CONFIG_USER_EMAIL
				  << ">" << modm::endl;
	MODM_LOG_INFO << "Last Commit:" << modm::endl;
	MODM_LOG_INFO << "Abbreviated SHA: " << MODM_GIT_SHA_ABBR << modm::endl;
	MODM_LOG_INFO << "Subject:         " << MODM_GIT_SUBJECT << modm::endl;
	MODM_LOG_INFO << modm::endl << "Author:" << modm::endl;
	MODM_LOG_INFO << "Name:      " << MODM_GIT_AUTHOR << modm::endl;
	MODM_LOG_INFO << "Email:     " << MODM_GIT_AUTHOR_EMAIL << modm::endl;
	MODM_LOG_INFO << "Date:      " << MODM_GIT_AUTHOR_DATE << modm::endl;
	MODM_LOG_INFO << "Timestamp: " << MODM_GIT_AUTHOR_DATE_TIMESTAMP << modm::endl;
	MODM_LOG_INFO << modm::endl << "File Status:" << modm::endl;
	MODM_LOG_INFO << "Mod " << MODM_GIT_MODIFIED << " Add " << MODM_GIT_ADDED << " Del "
				  << MODM_GIT_DELETED;
	MODM_LOG_INFO << " Ren " << MODM_GIT_RENAMED << " Cop " << MODM_GIT_COPIED << " Unt "
				  << MODM_GIT_UNTRACKED << modm::endl;
	MODM_LOG_INFO << modm::endl;

	const uint8_t boardId = readBoardId();
	const uint8_t nodeId = 2 * boardId;
	MODM_LOG_INFO.printf("Board ID: %d\n", boardId);
	MODM_LOG_INFO.printf("Canopen Node ID: %d\n", nodeId);

	Board::MotorBridge::GateDriverEnable::set();
	RF_CALL_BLOCKING(gateDriver.initialize());
	RF_CALL_BLOCKING(gateDriver.commit());

	Board::Motor::initialize();
	Board::Motor::MotorTimer::start();
	Board::MotorCurrent::setCurrentLimit(0xFFFF);  // Set current limit to 100%

	Motor0.initializeHall();

	Board::CanBus::Can::setStandardFilter(0, Board::CanBus::Can::FilterConfig::Fifo0,
										  modm::can::StandardIdentifier(0),
										  modm::can::StandardMask(0));

	Board::CanBus::Can::setExtendedFilter(0, Board::CanBus::Can::FilterConfig::Fifo0,
										  modm::can::ExtendedIdentifier(0),
										  modm::can::ExtendedMask(0));

	CanOpen::initialize(nodeId, micromotorId);
	auto lastMessage = modm::Clock::now();

	MODM_LOG_INFO << "Starting App Main Loop..." << modm::endl;
	while (1)
	{
		auto now = modm::Clock::now();
		using Can = Board::CanBus::Can;
		while (Can::isMessageAvailable())
		{
			modm::can::Message message;
			Can::getMessage(message);
			CanOpen::processMessage(message, Board::CanBus::Can::sendMessage);
			lastMessage = now;
			// MODM_LOG_INFO << modm::hex << message.getIdentifier() << modm::endl;
		}

		Motor0.update(Board::CanBus::Can::sendMessage);
		CanOpen::update(Board::CanBus::Can::sendMessage);
		/*if ((now - lastMessage) >= noMessageTimeout)
		{
			MODM_LOG_ERROR << "No messages! Resetting...\n" << modm::endl;
			break;
		}
		if (MotorState0::resetMotor_)
		{
			MODM_LOG_ERROR << "Resetting...\n" << modm::endl;
			break;
		}*/

		if (debugTimer.execute())
		{
			/*MODM_LOG_DEBUG << "MotorState:\n"
						   << "Max Current: " << MotorState0::maxCurrent_ << "\n"
						   << "Commanded Current: " << CurrentControl<0>::commandedCurrent_ << "\n"
						   << "Target Current: " << CurrentProtocol<0>::targetCurrent_ << "\n"
						   << "Unoriented Current: " << MotorState0::unorientedCurrent_ << "\n"
						   << "Oriented Current: " << MotorState0::orientedCurrent_ << "\n"
						   << "Commanded Velocity: " << VelocityProtocol<0>::commandedVelocity_
						   << "\n"
						   << "Actual Velocity: " << MotorState0::actualVelocity_.getValue() << "\n"
						   << "Commanded Position: " << PositionProtocol<0>::commandedPosition_
						   << "\n"
						   << "Actual Position: " << MotorState0::actualPosition_ << "\n"
						   << "Mode: " << MotorState0::mode_ << "\n"
						   << "Charge: " << MotorState0::currentCharge_ << "\n"
						   << "PWM: " << MotorState0::outputPWM_ << modm::endl;*/
		}
	}

	return 0;
}

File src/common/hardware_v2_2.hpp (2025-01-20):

/*
 * Copyright (C) 2019 Raphael Lehmann <raphael@rleh.de>
 * Copyright (C) 2021 Christopher Durand
 *
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
 * You should have received a copy of the GNU General Public License
 * along with this program.  If not, see <http://www.gnu.org/licenses/>.
 */

#ifndef HARDWARE_V2_HPP
#define HARDWARE_V2_HPP

#include <modm/platform.hpp>
#include <modm/architecture/interface/clock.hpp>
#include <modm/platform/uart/uart_hal_1.hpp>
#include <modm/platform/uart/uart.hpp>
#include <modm/processing/timer.hpp>

#include <librobots2/motor/motor_bridge.hpp>

using namespace modm::platform;
using namespace std::chrono_literals;

namespace Board
{
using namespace modm::literals;

constexpr uint32_t Version_Major = 2;
constexpr uint32_t Version_Minor = 2;
#define MICRO_MOTOR_HAS_ADC_W

/// STM32G474RE running at 170MHz generated from the internal 16MHz crystal
// Dummy clock for devices
struct SystemClock
{
	static constexpr uint32_t Frequency = 170_MHz;
	static constexpr uint32_t Ahb1 = Frequency;
	static constexpr uint32_t Ahb2 = Frequency;
	static constexpr uint32_t Apb1 = Frequency;
	static constexpr uint32_t Apb2 = Frequency;

	static constexpr uint32_t Cordic = Ahb1;
	static constexpr uint32_t Crc = Ahb1;
	static constexpr uint32_t Dma = Ahb1;
	static constexpr uint32_t Dma1 = Dma;
	static constexpr uint32_t Dma2 = Dma;
	static constexpr uint32_t DmaMux = Dma;
	static constexpr uint32_t Fmac = Ahb1;

	static constexpr uint32_t Adc = Ahb2;
	static constexpr uint32_t Adc1 = Adc;
	static constexpr uint32_t Adc2 = Adc;
	static constexpr uint32_t Adc3 = Adc;
	static constexpr uint32_t Adc4 = Adc;
	static constexpr uint32_t Adc5 = Adc;
	static constexpr uint32_t Dac = Ahb2;
	static constexpr uint32_t Dac1 = Dac;
	static constexpr uint32_t Dac2 = Dac;
	static constexpr uint32_t Dac3 = Dac;
	static constexpr uint32_t Dac4 = Dac;
	static constexpr uint32_t Rng = Ahb2;

	static constexpr uint32_t Can = Apb1;
	static constexpr uint32_t Fdcan1 = Can;
	static constexpr uint32_t Fdcan2 = Can;
	static constexpr uint32_t Fdcan3 = Can;
	static constexpr uint32_t I2c = Apb1;
	static constexpr uint32_t I2c1 = I2c;
	static constexpr uint32_t I2c2 = I2c;
	static constexpr uint32_t I2c3 = I2c;
	static constexpr uint32_t I2c4 = I2c;
	static constexpr uint32_t Lptim = Apb1;
	static constexpr uint32_t Lpuart = Apb1;
	static constexpr uint32_t Rtc = Apb1;
	static constexpr uint32_t Spi2 = Apb1;
	static constexpr uint32_t Spi3 = Apb1;
	static constexpr uint32_t Uart4 = Apb1;
	static constexpr uint32_t Uart5 = Apb1;
	static constexpr uint32_t Usart2 = Apb1;
	static constexpr uint32_t Usart3 = Apb1;
	static constexpr uint32_t Usb = Apb1;
	static constexpr uint32_t Apb1Timer = Apb1 * 1;
	static constexpr uint32_t Timer2 = Apb1Timer;
	static constexpr uint32_t Timer3 = Apb1Timer;
	static constexpr uint32_t Timer4 = Apb1Timer;
	static constexpr uint32_t Timer5 = Apb1Timer;
	static constexpr uint32_t Timer6 = Apb1Timer;
	static constexpr uint32_t Timer7 = Apb1Timer;

	static constexpr uint32_t Sai1 = Apb2;
	static constexpr uint32_t Spi1 = Apb2;
	static constexpr uint32_t Usart1 = Apb2;
	static constexpr uint32_t Apb2Timer = Apb2 * 1;
	static constexpr uint32_t Timer1 = Apb2Timer;
	static constexpr uint32_t Timer8 = Apb2Timer;
	static constexpr uint32_t Timer15 = Apb2Timer;
	static constexpr uint32_t Timer16 = Apb2Timer;
	static constexpr uint32_t Timer17 = Apb2Timer;
	static constexpr uint32_t Timer20 = Apb2Timer;

	static bool inline enable()
	{
		Rcc::enableInternalClock();  // 16MHz
		Rcc::PllFactors pllFactors{
			.pllM = 4,   //  16MHz / M= 4 ->   4MHz
			.pllN = 85,  //   4MHz * N=85 -> 340MHz
			.pllR = 2,   // 336MHz / R= 2 -> 170MHz = F_cpu
		};
		Rcc::enablePll(Rcc::PllSource::InternalClock, pllFactors);
		// set flash latency for 170MHz
		Rcc::setFlashLatency<Frequency>();
		// switch system clock to PLL output
		Rcc::enableSystemClock(Rcc::SystemClockSource::Pll);
		Rcc::setAhbPrescaler(Rcc::AhbPrescaler::Div1);
		// APB1 has max. 170MHz
		Rcc::setApb1Prescaler(Rcc::Apb1Prescaler::Div1);
		Rcc::setApb2Prescaler(Rcc::Apb2Prescaler::Div1);
		// update frequencies for busy-wait delay functions
		Rcc::updateCoreFrequency<Frequency>();

		Rcc::setCanClockSource(Rcc::CanClockSource::Pclk);

		return true;
	}
};

namespace Ui
{
using LedRed = GpioA4;    // DAC1
using LedGreen = GpioA5;  // DAC2

using DebugUartTx = GpioB6;
using DebugUartRx = GpioB7;
using DebugUart = BufferedUart<UsartHal1>;
static constexpr uint32_t DebugUartBaudrate = 460800_Bd;

inline void
initializeDebugUart()
{
	DebugUart::connect<DebugUartTx::Tx, DebugUartRx::Rx>();
	DebugUart::initialize<SystemClock, DebugUartBaudrate>();
}

/**
 * Should be used mutually exclusive to `initializeDac`
 *
 * Initializes the LEDs as standard outputs
 */
inline void
initializeLeds()
{
	LedRed::setOutput(false);
	LedGreen::setOutput(false);
}
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

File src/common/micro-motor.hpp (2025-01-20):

#pragma once
#include "hardware.hpp"
#include <tuple>
#include <cmath>
#include <array>
#include <modm/debug/logger.hpp>
namespace micro_motor
{

inline void
initialize()
{
	using MotorTimer = Board::Motor::MotorTimer;

	MotorTimer::enableInterruptVector(MotorTimer::Interrupt::Update, true, 5);
	MotorTimer::enableInterrupt(MotorTimer::Interrupt::Update);
}

constexpr std::tuple<float, float>
clarkeTransform(float u, float v)
{
	constexpr float one_by_sqrt3 = (float)(1.0 / std::sqrt(3.0));
	constexpr float two_by_sqrt3 = (float)(2.0 / std::sqrt(3.0));

	return {u, u * one_by_sqrt3 + v * two_by_sqrt3};
}

constexpr float
convertAdcToCurrent(uint16_t adcValue)
{
	constexpr float ShuntResistance = 5e-3;
	constexpr float CurrentGain = 50;
	constexpr float ReferenceVoltage = 2.9;
	constexpr float FummelKonstante = 1.0f;
	constexpr uint16_t AdcCounts = (1 << 12) - 1;

	const float adcVoltage = adcValue * (ReferenceVoltage / AdcCounts);
	const float current =
		((adcVoltage - (ReferenceVoltage / 2.0f)) / (CurrentGain * ShuntResistance));
	return current * FummelKonstante;
}

constexpr uint16_t
convertCurrentToCurrentLimit(float current)
{
	constexpr float ShuntResistance = 5e-3;
	constexpr float CurrentGain = 50;
	constexpr float ReferenceVoltage = 2.9;
	constexpr uint16_t AdcCounts = (1 << 12) - 1;
	const float adcVoltage =
		(current * CurrentGain * ShuntResistance) + (ReferenceVoltage / 2.0f);
	const float adcValue = adcVoltage / (ReferenceVoltage / AdcCounts);
	return (uint16_t)std::clamp(adcValue,0.0f,4095.0f);
}

inline void
setCurrentLimitAmps(float limit)
{
	uint16_t limit_12_bit = convertCurrentToCurrentLimit(limit) & 0x0FFF;
	DAC3->DHR12R1 = limit_12_bit;
	DAC3->DHR12R2 = limit_12_bit;
}

void
updateADC();

std::array<float, 3>
getADCCurrents();

std::array<uint16_t, 3>
getADCValues();

};  // namespace micro_motor

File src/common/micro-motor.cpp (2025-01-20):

#include "micro-motor.hpp"
#include <cstdint>

namespace micro_motor
{
static uint16_t adc_u_value = 0x7ff;
static uint16_t adc_v_value = 0x7ff;
#ifdef MICRO_MOTOR_HAS_ADC_W
static uint16_t adc_w_value = 0x7ff;
#endif

std::array<uint16_t, 3>
getADCValues()
{
	#ifdef MICRO_MOTOR_HAS_ADC_W
	return {adc_u_value, adc_v_value, adc_w_value };
	#else
	int adc_w_value = -((int)adc_u_value - 0x7ff) - ((int)adc_v_value - 0x7ff);

	return {adc_u_value, adc_v_value, (uint16_t)(adc_w_value + 0x7ff)};
	#endif
}

std::array<float, 3>
getADCCurrents()
{
	float u = convertAdcToCurrent(adc_u_value);
	float v = convertAdcToCurrent(adc_v_value);
	#ifdef MICRO_MOTOR_HAS_ADC_W
	float w = convertAdcToCurrent(adc_w_value);
	#else
	float w = -u - v;
	#endif
	return {u, v, w};
}

void
updateADC()
{
	using AdcU = Board::MotorCurrent::AdcU;
	using AdcV = Board::MotorCurrent::AdcV;

	adc_u_value = AdcU::getValue();
	adc_v_value = AdcV::getValue();

	AdcV::acknowledgeInterruptFlags(AdcV::InterruptFlag::EndOfRegularConversion |
									AdcV::InterruptFlag::EndOfSampling |
									AdcV::InterruptFlag::Overrun);
	AdcU::acknowledgeInterruptFlags(AdcU::InterruptFlag::EndOfRegularConversion |
									AdcU::InterruptFlag::EndOfSampling |
									AdcU::InterruptFlag::Overrun);

#ifdef MICRO_MOTOR_HAS_ADC_W
	using AdcW = Board::MotorCurrent::AdcW;
	adc_w_value = AdcW::getValue();
	AdcW::acknowledgeInterruptFlags(AdcW::InterruptFlag::EndOfRegularConversion |
									AdcW::InterruptFlag::EndOfSampling |
									AdcW::InterruptFlag::Overrun);
#endif
}

}  // namespace micro_motor

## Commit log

2017-09-14 initial µmotor design
    [µmotor-can.sch, µmotor-encoder.sch, µmotor-microcontroller.sch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]
2017-09-14 add STM32CubeMX file, STM32F042 pinout
2018-01-05 add DRV8323S kicad symbol lib
2018-01-06 add FDMD82xx kicad symbol lib
2018-01-06 add generated (up-to-date) STM32 kicad symbol lib
2018-01-06 add STM32CubeMX file, STM32L432KC (UFQFPN32) pinout
2018-01-06 second design: STM32L432KC µC with DRV8323S gate driver and FDMD82xx FETs
    [µmotor-can.sch, µmotor-encoder.sch, µmotor-microcontroller.sch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]
2018-01-06 add STM32CubeMX file, STM32L433CCUx (UFQFPN48) pinout
2018-02-04 update µC pinout, motor driver, CubeMX, add 3V3 regulator and temperature sensor
    [µmotor-can.sch, µmotor-encoder.sch, µmotor-microcontroller.sch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]
2018-02-05 layout: components placed
    [µmotor-can.sch, µmotor-encoder.sch, µmotor-microcontroller.sch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]
2018-02-05 layout: routing finished
    [µmotor-microcontroller.sch, µmotor.kicad_pcb]
2018-02-05 layout: minor improvements
    [µmotor-can.sch, µmotor-encoder.sch, µmotor-microcontroller.sch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]
2018-02-05 layout: improvements and silkscreen
    [µmotor-can.sch, µmotor-encoder.sch, µmotor-microcontroller.sch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]
2018-02-05 layout: export gerber
    [µmotor-B.Cu.gbl, µmotor-B.Mask.gbs, µmotor-B.Paste.gbp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]
2018-02-06 add DRV8323 input cap, improve board outline
    [PCB_Outline_rev1.dxf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]
2018-02-06 layout: improvements
    [µmotor-B.Cu.gbr, µmotor-B.Mask.gbr, µmotor-B.Paste.gbr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]
2018-02-10 increase via and track sizes
    [µmotor-B.Cu.gbr, µmotor-B.Mask.gbr, µmotor-B.Paste.gbr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]
2018-04-14 [software] Test: Blink
    [project.cfg]
2018-05-05 [software] replace xpcc with modm
    [project.cfg]
2018-05-06 [software] test: pwm generation
2018-05-08 [software] test: blink two leds
2018-05-16 [software] add Drv832x driver
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2018-05-22 [software] hardware.hpp: DebugUart baudrate 460800; Spi Miso external pull-up
2018-05-22 [software] Drv832x driver: fixes
2018-05-22 [software] Drv832x driver reworked
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2018-05-22 [drv832x_testboard] add schematic
    [drv832x_testboard.kicad_pcb, drv832x_testboard.sch, µmotor-can.sch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]
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2018-07-11 [software] test DC motor: add ADC current measurement
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2018-08-10 [ci] add DC and BLDC motor test to CI
2018-09-04 Fix BLDC commutation logic
    [main.cpp]
2018-09-23 Remove unfinished DRV832x testboard
    [drv832x_testboard.kicad_pcb, drv832x_testboard.sch, µmotor-can.sch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]
2018-09-23 Add macro-motor dev board schematic
    [macro-motor-can.sch, macro-motor-encoder.sch, macro-motor-microcontroller.sch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]
2018-09-24 macro-motor: Finish dev board schematic
    [macro-motor-can.sch, macro-motor-encoder.sch, macro-motor-microcontroller.sch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]
2018-09-24 macro-motor: PCB Layout
    [macro-motor-B.Cu.gbr, macro-motor-B.Mask.gbr, macro-motor-B.SilkS.gbr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]
2018-09-24 macro-motor: PCB Layout finished, silkscreen
    [macro-motor-B.Cu.gbr, macro-motor-B.Mask.gbr, macro-motor-B.Paste.gbr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]
2018-09-24 macro-motor: Minor fixes
    [macro-motor-B.Cu.gbr, macro-motor-B.Mask.gbr, macro-motor-B.Paste.gbr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]
2018-09-25 macro-motor: add BOM (csv)
    [macro-motor.csv]
2018-09-25 macro-motor: Minor fixes, remove hole at (0,0)
    [macro-motor-B.Cu.gbr, macro-motor-B.Mask.gbr, macro-motor-B.SilkS.gbr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]
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2019-09-20 micro-motor-v2: kicad project started
    [Can.sch, Microcontroller.sch, Motordriver.sch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]
2019-09-20 micro-motor-v2: Schematic continued
    [Can.sch, Microcontroller.sch, Motordriver.sch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]
2019-09-20 micro-motor-v2: Fix DRV8323/DRV8320 libs
2019-09-20 micro-motor-v2: Schematic finished
    [Can.sch, Microcontroller.sch, Motordriver.sch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]
2019-09-20 micro-motor-v2: layout: components placed
    [Can.sch, Motordriver.sch, Power_Supply.sch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]
2019-09-23 micro-motor-v2: More capacitors, outline corners
    [Motordriver.sch, micro-motor-v2.kicad_pcb]
2019-09-23 micro-motor-v2: Layout...
    [Can.sch, Microcontroller.sch, Motordriver.sch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]
2019-10-10 micro-motor-v2: Layout finished
    [Motordriver.sch, micro-motor-v2.kicad_pcb]
2019-10-10 micro-motor-v2: Layout Silkscreen
    [micro-motor-v2.kicad_pcb]
2019-10-19 micro-motor-v2: BOM
    [micro-motor-v2.csv]
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2019-11-02 Move micro-motor-v1 pcb to subfolder
    [PCB_Outline_rev1.dxf, µmotor-can.sch, µmotor-encoder.sch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]
2019-11-02 Remove gerber files
    [macro-motor-B.Cu.gbr, macro-motor-B.Mask.gbr, macro-motor-B.Paste.gbr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]
2021-07-31 PCB: micro-motor-v2.1
    * Replace TPS82150 with LMZM23601
    * Add 1uF capacitor to STM32 VREFBUF output pin
    * Add RC filters (10nF / 10Ω) to encoder input
    [Can.sch, Microcontroller.sch, Motordriver.sch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]
2021-11-17 CI: Add kibot job to generate schematics and PCB PDFs
2021-11-17 Fix KiCAD lib file syntax for kibot
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2021-11-19 Use more lbuild!
    [micro-motor.xml]
2021-11-19 [sw][test] fix xml and includes for blinky
    [main.cpp]
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2022-04-18 [app+test] Replace deprecated modm::delayMilliseconds() with modm::delay_ms()
    [main.cpp]
2022-04-18 Fix pwm timer frequency
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2022-04-18 Fix functions call from library
    [main.cpp]
2022-04-18 Separate UI::init.() fct - using leds either as IO or via DAC
2022-04-18 Seperate debug uart init from dac/led init; fix all tests
    [main.cpp]
2022-04-18 Fix bugs test applications
    [main.cpp]
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2022-04-18 Hacked application for controlling 1 DC motor with motor-can
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2022-10-16 BLDC block commutation example with canopen interface
    [micro-motor.xml]
2022-10-16 Fix reading hall state
2023-01-20 [canopen] Added tests for canopen bldc
    [micro-motor-board.xml, micro-motor-hosted.xml, micro-motor.xml]
2023-01-20 [canopen] Fixed include paths
    [main.cpp]
2023-01-20 [canopen] Made velocity PID parameters writeable over can
2023-01-20 [canopen] Moved test related stuff out of src
    [micro-motor-board.xml, micro-motor.xml]
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2023-01-21 [canopen] Replace Pos-Error with proper object
    [main.cpp]
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2023-03-26 [canopen] Fix unused parameter warnings
    [main.cpp]
2023-03-28 [canopen] fix missing include in pwm protocol
2023-04-16 [app] assign boardID and nodeID based on hardwareID
2023-04-20 Add timeout to device reset
    [main.cpp]
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2023-04-24 Add Reset Register to reset motors
    [main.cpp, motor_state.hpp]
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2023-04-30 Fix motor being instantly reenabled
2023-05-01 Move motor independent stuff to its own repo
    [micro-motor.xml]
2023-05-03 Move scons dependency out of micro-motor.xml
    [micro-motor.xml]
2023-05-08 Move motor-canopen to librobots2
    [micro-motor.xml]
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2023-05-19 Fix adcs not returning values
    [main.cpp, micro-motor.cpp, micro-motor.hpp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]
2023-05-22 chaneg modm-canopen module, implement sim current
    [micro-motor.xml]
2023-06-21 app: made current-control work somewhat
    fix inconsistent commutation
    [main.cpp, micro-motor.cpp, micro-motor.hpp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]
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2023-07-11 made necessary changes for V2.2, missing DRC
    [Can.kicad_sch, Can.sch, Microcontroller.kicad_sch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]
2023-07-11 solved most critical DRC issues
    [micro-motor-v2.2.kicad_pcb]
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2023-08-08 ready to order
    [Can.kicad_sch, Microcontroller.kicad_sch, Motordriver.kicad_sch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]
2023-08-15 app: reenable timeout reset
    [main.cpp]
2023-08-15 commander: Fix Object names
    [main.cpp]
2023-09-26 Hopefully fix ADC initialization
2023-10-14 Boot camp: fix current control
    [main.cpp, motor.cpp]
2023-10-14 Fix wrong current being set
    [main.cpp]
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2024-02-11 Switch season2023 to submodules
    [micro-motor.xml]
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2024-02-12 Fix commander not correctly setting PWM
    [main.cpp]
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2024-02-20 Fix stupid error in relay_analyzer
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2024-02-29 [motor-tuner] Fix State setup
    [main.cpp]
2024-02-29 [canopen_bldc_hosted] Fix warning, update motor config
    [main.cpp]
2024-02-29 [motor_tuner] Fix obviuous bugs in relay_analyzer
    [main.cpp, motor_state.hpp]
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2024-03-08 Fix outdated currentLimit definition
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2024-03-12 Basically revert to PWM control
    [main.cpp, micro-motor.hpp, state.hpp]
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2024-06-06 Fix waiting in test-firmware
    [run_forward.cpp, test_current_limit.cpp]
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2024-11-22 [canopen_hosted] Fix hosted operation
    [main.cpp]
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2025-02-11 [CI] Disable PDF generation on failed ERC with kicad 8
2025-02-11 [CI] Fix CI trigger for Kicad
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2025-02-11 [CI] Attempt to fix ERC
    [Can.kicad_sch, Can.sch, Microcontroller.kicad_sch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]
2025-02-16 Fix assembly pdf

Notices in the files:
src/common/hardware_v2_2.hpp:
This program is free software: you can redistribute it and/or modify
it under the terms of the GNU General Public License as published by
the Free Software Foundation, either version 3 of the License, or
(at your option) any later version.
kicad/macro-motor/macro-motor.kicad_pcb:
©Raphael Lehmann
